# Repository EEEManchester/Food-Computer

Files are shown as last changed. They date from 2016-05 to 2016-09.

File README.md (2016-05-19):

# Food-Computer
A project to create a controlled indoor growing environment using embedded systems, sensors and control

Our plan is to build a www.eee.manchester.ac.uk  prototype version of the MIT OpenAgri "Food Computer" with an idea to scaling the design out in the future. 

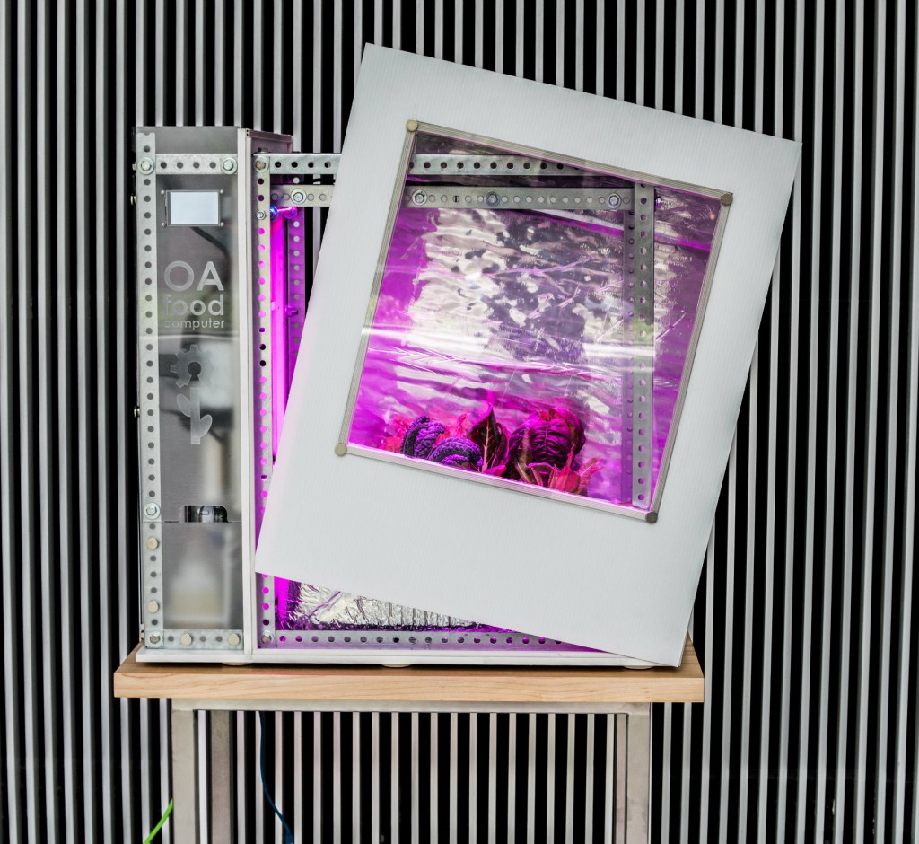
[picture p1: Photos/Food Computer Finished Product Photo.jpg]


####Please see our Github Wiki for all information on the project

Code and hardware are forked from https://github.com/OpenAgInitiative

For more information see here
https://www.media.mit.edu/special/groups/open-ag

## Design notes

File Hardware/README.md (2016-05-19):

# gro-hardware
All things related to assembling a food computer. CAD Models, Build Manual, Bill of Materials, etc.

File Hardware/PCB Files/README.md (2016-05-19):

# gro-PCB
Robusto board, RHC12, and RHC12-BTA schematics/pcbs

Robusto is split into two parts, Part1 and Part2.  RHC12 is the base connector that works with Grove and 0.1" spaced header, RHC12-BTA is for a BTA connector.  

##THESE PCBS HAVE BEEN CONVERTED TO ALTIUM DESIGNER BY EEE MANCHESTER FROM EAGLE BOARD FILES CREATED AT MIT

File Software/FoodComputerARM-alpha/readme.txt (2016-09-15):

Alpha version; tested only on ARM mbed Nucleo F401RE board.
Can be found here: 
https://developer.mbed.org/users/AfdhalAtiffTan/code/FoodComputerARM-alpha/

It meant to replace Arduino boards and use ARM processor instead.
It serves the same purpose as "Food_Computer_Draft_V2" (with compatible pinout).

Differences:
-It uses MODBUS RTU instead of non-standard uart protocol.
-Analogue pins are 3.3V, make sure to divide the voltage first.
-Has three debugging LEDs.
-Some of the sensors data were scaled by 100;

Logs:
-Tried to use RTOS, but failed because the software-serial library can't handle it (took a long time to figure this out).

-Because RTOS failed, it uses Ticker instead.

-Most of the libraries are download from mbed community.

-The modbus library was a modified Arduino library.

-Programming using ST-Link achieves more consistent results.

-Sometimes, the online compiler gives peculiar result, try to compile using Keil (by exporting it to local pc). In other words, sometimes, both online and Keil compiler can give very different behaviour (such as failed I2C etc.). 

-If uses mbed to upload the program, don't forget to manually reset the ARM board by pushing the reset button before every each upload. Not too sure why but it was discovered that it gives more predictable result.

-Reconnecting the USB cable and Clicking on "Compile" then "Compile All" multiple times sometimes helps.

-If errors were found, sometimes clicking the "Update" and "Update All" helps. 

-All of the communications tested only on oscilloscope, not on the actual sensors.

-The program will not start without CO2 sensor because of the blocking-call used.

-Don't request data faster than 1 second because the update rate is 100ms (not including sensors).

-Searching library/program on the mbed IDE gives incomplete results. Better to use mbed website or Google.

Notes:
-Program here was exported from mbed environment.
-The program is far from perfect, bugs might exists. 
-It was not written to look proper, yet.
-The code may look ugly as it was coded using the glue method.
-If the Raspberry Pi appears not to be stuck, add a 5 seconds delay after relay initialisation. Fault from: Modbus library.

To-dos:
-Proper documentation and Doxygen.
-Format the code so that it looks more professional and manageable.
-Test all communication on all sensors.

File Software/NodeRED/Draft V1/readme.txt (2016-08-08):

This Draft V1 is meant for backup purposes. It is far from ideal and may contains a lot of bugs.

It should be able to control arduino (or any capable microcontroller) via serial communication (onboard usb-ttl).
 
It has:
-simple relay control
-simple relay timer
-non-standard serial communication (simple one-character ascii commands)
-charts for sensors (polled every 10 seconds)
-gauges for sensor (polled every 10 seconds)
-simple webcam interface (just live stream, no capture yet)
-simple close-loop control (bang-bang controller) for lights, humidity and temperature
-simple MQTT client
-basic system control (Pi reboot and shutdown)

To use it, simply install nodered by using [Peter Scargill]'s scripts:

https://bitbucket.org/snippets/scargill/ayAG6/include-for-jessie-script-call-it

https://bitbucket.org/snippets/scargill/L8zjE/raspbian-jessie-and-node-red-script-for

For installation explanation by [Peter Oakes] (near minute 9:30):
https://www.youtube.com/watch?v=uyx2KZNxhe4

The installation should include all required libraries. If not, they can be found on:
http://flows.nodered.org/ or
https://www.npmjs.com/

Optional: "Motion" package must be installed on the Pi in order to use the usb webcam:
https://pimylifeup.com/raspberry-pi-webcam-server/

After installation, node-red can be access via:
main interface: http://localhost:1880
web UI: http://localhost:1880/ui

Then, import the json file (flows_FoodComputerPi.json) by copying and paste it into (localhost:1880)>(Menu)>(Import)>(Clipboard)

Optional: Port forwarding, to allow external access.

Future version:
-Should include modbus-rtu. Credit: [Sam Walsh].

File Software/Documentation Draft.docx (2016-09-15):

# Microcontroller Connections

Any microcontroller that has the ability to interface with all of the listed sensors can be used, but, at the moment (August 2016), only two test programs were pushed on this repository:

- “Food_Computer_Draft_V2” sketch: For Arduino based boards (such as Uno, Mega, Nano, etc).
- “FoodComputerARM-alpha” program: For mbed-enabled ARM-based boards (tested only on Nucleo F401RE) – uses.

Feel free to use any other suitable microcontroller as needed.

Main tasks of the microcontroller are reading all sensors and controlling relays via UART.

No intelligence implemented yet (such as fail-safe, auto scheduling, RTC based timer, closed-loop control, etc). All controls are manually controlled.

Actuators were controlled by Relay modules.

Sensors Used:

- Carbon Dioxide Sensor (http://www.co2meter.com/products/cozir-0-2-co2-sensor): COZIR Ambient 2/5/10K CO2 Sensor [UART]
- Air Humidity and Temperature Sensor (https://www.seeedstudio.com/item_detail.html?p_id=838): Grove - Temperature&Humidity Sensor Pro (DHT22) [AM2302]
- Light Intensity Sensor (https://www.seeedstudio.com/item_detail.html?p_id=1281): Grove - Digital Light Sensor (TSL2561) [I2C]
- Water pH Sensor (http://www.dfrobot.com/index.php?route=product/product&product_id=1025): Gravity: Analog pH Meter Kit [ADC]
- Temperature compensated Water Conductivity Sensor (http://www.dfrobot.com/index.php?route=product/product&product_id=1123): Gravity:Analog Electrical Conductivity Meter (With Temperature Compensation (http://www.dfrobot.com/index.php?route=product/product&product_id=689)) [ADC for EC and 1-Wire for DS18B20 thermometer]

Both analogue sensors have voltage divider (from 5V to 3.3V) hidden in cables (heat shrink tube) to avoid damaging 3.3V ARM board (Arduino runs on 5V). The resistors used were 1% tolerance and 3.3kR, 100R and 1.6kR all in series.

Physical Pinouts:

Both Arduino and mbed uses Arduino’s pin convention, A and D stands for Analog and Digital pin respectively.

(Compatible with “Food_Computer_Draft_V2” and “FoodComputerARM-alpha”)

A0 – Water pH Sensor (Analog) – 5V

A1 – Water Electrical Conductivity Sensor (Analog) – 5V

A2 – Shell Switch (Digital) – 5V or 3.3V on ARM

A3 – Window Switch (Digital) – 5V or 3.3V on ARM

D0 – Reserved for USB/UART communication (RX)

D1 – Reserved for USB/UART communication (TX)

D2 – Air Humidity and Temperature Sensor (DHT22) – 5V

D3 – Water Temperature Sensor (OneWire) – 5V

D4 – Relay0 (Active Low) – AC – Grow Light - 240V

D5 – Relay1 (Active Low) – AC – Water Pump - 240V

D6 – Relay2 (Active Low) – AC – Air Pump - 240V

D7 – Relay3 (Active Low) – AC – Air Pump - 240V

D8 – Relay4 (Active Low) – DC – Circulation Fan - 12V

D9 – Relay5 (Active Low) – DC – Ventilation Fan - 12V

D10 – Relay6 (Active Low) – DC – Strip Lights - 12V

D11 – Relay7 (Active Low) – DC – Air Humidifier - 5V

D12 – CO2 Sensor (RX) - 3.3V!

D13 – CO2 Sensor (TX) - 3.3V!

D14 – Light intensity sensor (SDA) – 5V

D15 – Light intensity sensor (SCL) – 5V

Connections were done via Grove Shield v2 (http://wiki.seeedstudio.com/wiki/Grove_-_Base_shield_v2).

If troubleshooting the connection via the connectors on the shield, the silkscreens on the PCB represent:

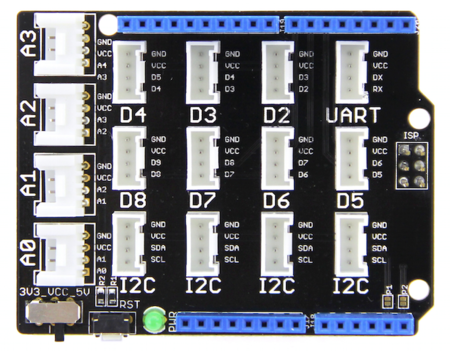
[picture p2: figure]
caption

Image credit: Google image search

Vcc switch was set 5V. RST button is useful especially if raspberry pi or the Modbus library stuck.

UART – 5V power to relay module 1

D2- Air Humidity and Temperature Sensor (DHT22)

D3 - Water Temperature Sensor (OneWire)

D4 – 5V power to relay module 2

A0 – pH Sensor

A1 – EC Sensor

A2 – Windows Switch Sensor

A3 – Shell Switch Sensor

I2C (any port would do) – Light Intensity Sensor

To reset the microcontroller board via Raspberry Pi, an open-collector npn switch was connected to GPIO BCM16 (or GPIO16 or pin 36) on the Pi.

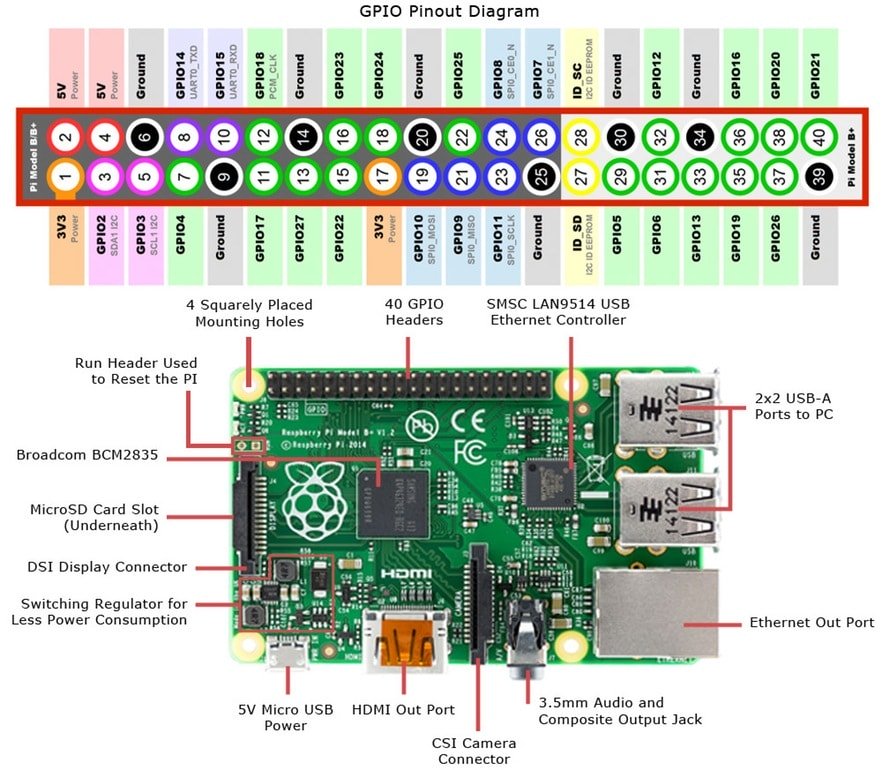
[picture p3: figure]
Image result for raspberry pi 3 pinout

Image credit: google image search

# Developed Firmwares:

As mentioned above, there are two firmwares listed in this repo:

Food_Computer_Draft_V2

Is a simple Arduino based “sketch”. It comes with simple Python PyQt based GUI that sends simple non-standard ascii-commands through USB/UART. Sensor readings were sent in CSV format.

The sketch is nothing but a combined libraries that read all attached sensors and send it to COM port.

FoodComputerARM-alpha

Developed using mbed compiler. Coded to be controlled by 9600 baud-rate MODBUS-RTU (credit: Sam). Sensor readings can be extracted by using Modbus register read command (http://www.simplymodbus.ca/FC03.htm).

The Nucleo-401RE board is configured as Modbus slave and its address is 01.

The register used are as follows:

Holding Register Address | Stored Data | Comment
01 | Carbon Dioxide Sensor (the sensor is also at 9600bps) | PPM Value
02 | Air Humidity Sensor (DHT22 protocol) | In % (scaled to x100)
03 | Air Temperature (via humidity sensor) | In Celcius (scaled to x100)
04 | Water Temperature (OneWire) | In Celcius (scaled to x100)
05 | Water Electrical Conductivity (Analogue) | In mS/cm (scaled to x100)
06 | Water pH Level (Analogue) | In pH (scaled to x100)
07 | Light Intensity (I2C) | Lux?
08 | Window Switch | Simple True/False
09 | Shell Switch (should be used for water level instead?) | Simple True/False
10 | Relays (should be changed in future so that individual relays has its own register) | Use this register to control relays (first bit is for first relay, second bit is for second relay, and so on)

The Modbus library works by periodically checks for request every 100ms. Meaning, any data transactions must be no faster than 100ms. This can be modified to run on separate thread, but, other library incompatibly issues will arise. Future revision should use a more robust Modbus library (UART interrupts?).

# Developed GUIs (PyQT-based)

- Simple UART
- Simple MQTT
- Simple Node-Red web UI (for ARM and Arduino)

(to be continued…)

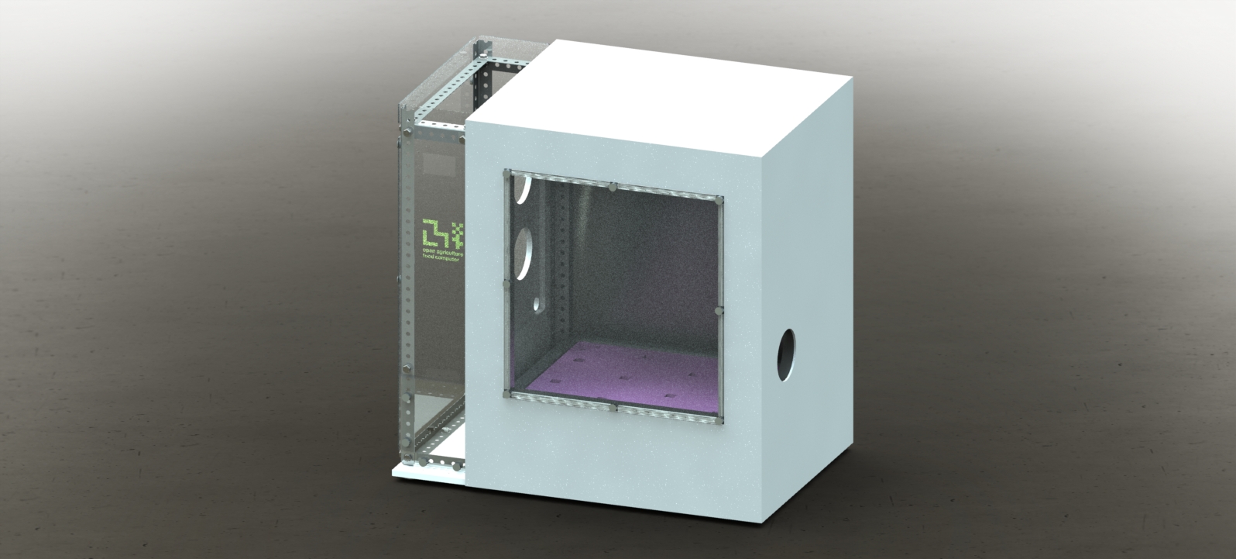
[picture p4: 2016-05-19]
Hardware/Food Computer CAD/RENDERS/Iso Closed.JPG

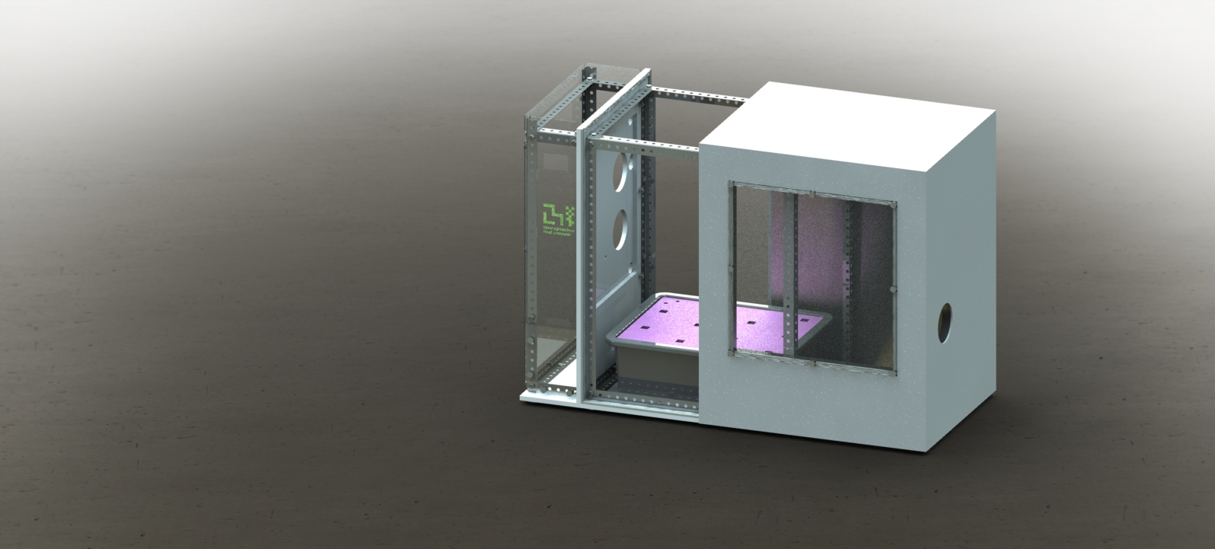
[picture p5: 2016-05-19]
Hardware/Food Computer CAD/RENDERS/Iso Brighter.JPG

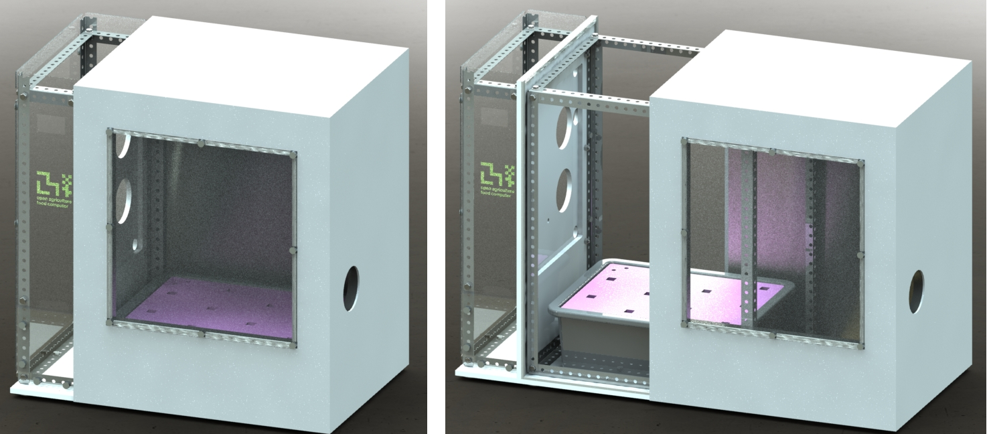
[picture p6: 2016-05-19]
Hardware/Food Computer CAD/RENDERS/Compilation.png

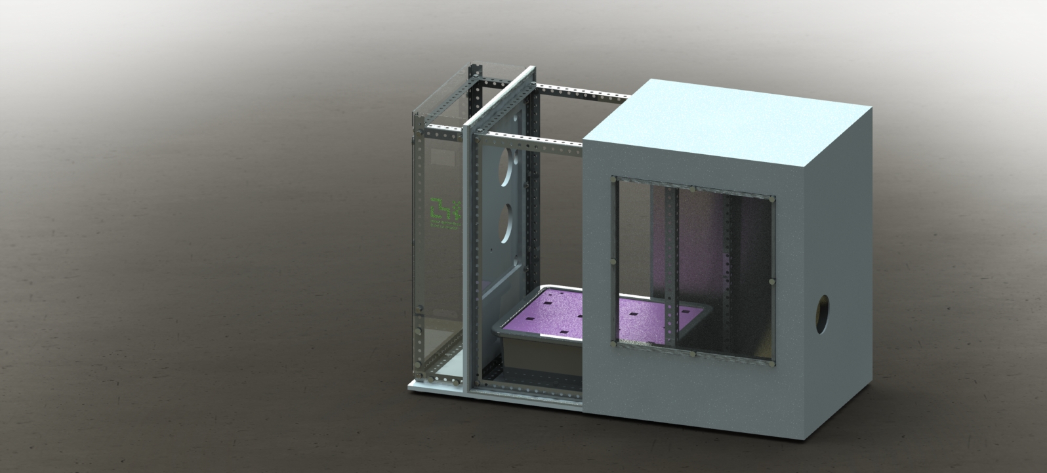
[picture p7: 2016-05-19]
Hardware/Food Computer CAD/RENDERS/Iso.JPG

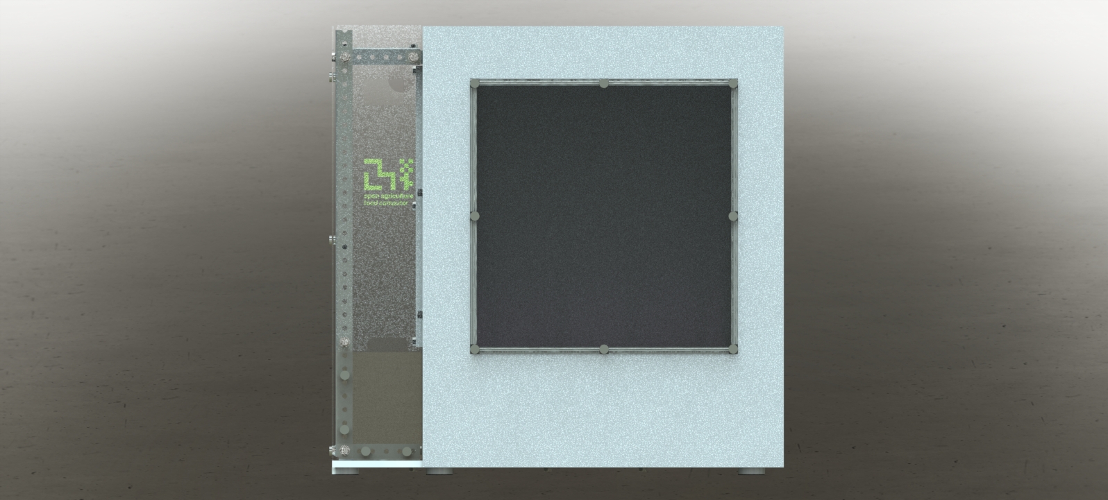
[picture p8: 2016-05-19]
Hardware/Food Computer CAD/RENDERS/Front Closed.JPG

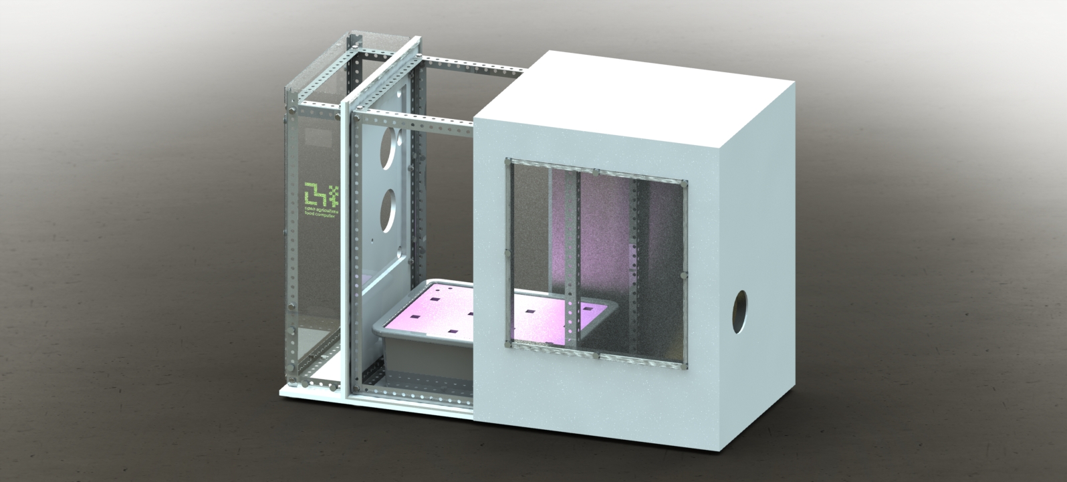
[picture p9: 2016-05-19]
Hardware/Food Computer CAD/RENDERS/Iso Brightest.JPG

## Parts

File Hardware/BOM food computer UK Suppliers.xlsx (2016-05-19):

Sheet: Motherboard University Supplier
Item Name | Distributor | Distributor's Item Name | Units | Cost per Unit ($) | Item Cost | Ordered
POWER
Power Strip (http://www.uk.insight.com/en-gb/productinfo/power-adapters/0003849924) | Insight | Belkin 6 Outlet Power Surge Protector | 1 | £9.26 | £9.26
Main Power Supply (https://www.amazon.co.uk/sourcingmap-Input-Output-Metallic-Supply/dp/B00E0K8LXO) | AmazonPrime | 12V 30A 360W Switching Power Supply for LED Strip Light | 1 | £20.10 | £20.10
BRAINS
Raspberry Pi 3 Essentials Kit (https://shop.pimoroni.com/products/raspberry-pi-3-essentials-kit?) | Pimoroni | CanaKit 5V 2.5A Raspberry Pi 2 Power Supply (UL Listed) | 1 | £52.00 | £52.00
Arduino Mega 2560 (http://uk.farnell.com/arduino/a000067/atmega2560-arduino-mega2560-rev3/dp/2212779) | Farnell | Arduino Mega 2560 R3 for Arduino | 1 | £28.76 | £28.76
Arduino Mega Protoshield (http://onecall.farnell.com/arduino/a000077/arduino-shield-proto-shield/dp/SC13010) | Farnell | ARDUINO A000077 ARDUINO SHIELD, PROTO SHIELD | 1 | £14.00 | £14.00
Grove Base Shield (http://www.seeedstudio.com/depot/Base-Shield-V2-p-1378.html) | SeeedStudio | Base Shield V2 | 1 | 8.9 | 8.9
Touchscreen Display (https://shop.pimoroni.com/products/pitft-plus-480x320-3-5-tft-touchscreen-for-raspberry-pi-pi-2-and-model-a-b) | Pimoroni | PiTFT - Assembled 480x320 3.5" TFT+Touchscreen for Raspberry Pi | 1 | £39.00 | £39.00
GPIO Cable (http://onecall.farnell.com/cyntech/ctlgpiopi-01/raspberry-pi-gpio-ribbon-100mm/dp/SC12819) | Farnell | GPIO ribbon cable for Raspberry Pi set with 2x13 stackable header and 2x13 box header | 1 | £1.19 | £1.19
VOLTAGE CONTROL
4-Channel Relay (https://www.amazon.co.uk/Shield-Module-channels-optocoupler-Arduino/dp/B00X3VRMPY) | AmazonPrime UK | JBtek 4 Channel DC 5V Relay Module for Arduino Raspberry Pi DSP AVR PIC ARM | 2 | £6.99 | £13.98
AC Relay 2 Plug Outlet (https://www.amazon.co.uk/Masterplug-NBS22UB-Brushed-Socket-Charger/dp/B00KMVYJX6) | AmazonPrime UK | Masterplug NBS22UB Brushed Steel Twin Socket with USB Charger | 2 | £14.95 | £29.90
AC Relay 2 gang back box (https://www.amazon.co.uk/Gang-Metal-Flush-Mount-Pattress/dp/B01BLFS8N8?rps=1) | AmazonPrime UK | 5x 2 GANG METAL BACK BOX | 1 | £7.99 | £7.99
LIGHTS
White LED Strip (https://www.amazon.co.uk/Waterproof-Flexible-Lights-3528-Daylight/dp/B00HSF66JO) | AmazonPrime UK | Triangle Bulbs T93007 - Waterproof Flexible LED Strip Light, 300 LED's, 3528 SMD, Pure White, 16.4 feet / 5M | 2 | £9.99 | £19.98
Grow LED Panel (https://www.amazon.co.uk/dp/B00W54BHO2?colid=E7891C74300P&coliid=I3MK2UTDFRU1HX) | AmazonPrime UK | Erligpowht 45W LED Red Blue Indoor Garden Plant Grow Light Hanging Light | 2 | £27.99 | £55.98
AIR CONDITIONING
Heater (https://www.amazon.co.uk/Honeywel-Personal-Heater/dp/B01BSEY5LQ) | AmazonPrime UK | HoneyWell Personal Ceramic Heater | 1 | £24.99 | £24.99
Humidifier (https://www.amazon.co.uk/FOME-Portable-Bottle-Humidifier-bottle/dp/B00X3GA5JO) | AmazonPrime UK | FOME Portable Bottle Cap Air Humidifier | 1 | £8.99 | £8.99
USB Wall Adapter (https://www.amazon.co.uk/PIXNOR-UK-plug-Output-Adapter-Charger/dp/B00IVC8U24) | AmazonPrime UK | PIXNOR 5V/2A UK-plug Dual USB Output AC Power Adapter Wall Charger | 3 | £4.99 | £14.97
Circulation/Vent Fans (https://www.amazon.co.uk/VIKINS-Delta-AFB1212VHE-cooling-Connector/dp/B01EURAYC2?s=computers) | AmazonPrime UK | VIKINS Delta AFB1212VHE 120mm X 38mm Very High Speed cooling Fan 2Pin 2 wire Connector 148 CFM NEW | 2 | £10.99 | £21.98
Fan Guards (https://www.amazon.co.uk/Silver-Axial-Protector-Finger-Guards/dp/B007PPEPJ0?s=computers) | AmazonPrime UK | 5 Pcs Silver Tone Axial Fan Grill Protector 12cm Metal Finger Guards | 1 | £5.43 | £5.43
Fan Louvres (https://www.amazon.co.uk/Kair-Gravity-Grille-Ventilation-DUCVKC243-BK/dp/B004X4RWJG) | AmazonPrime UK | Kair Gravity Grille - 100mm Round Spigot - Black - SYS-100 Ducting 4 inch Plastic Air Vent PVC Ventilation Duct Shutter Flap Non-Return Outlet Gravity Grill DUCVKC243-BK | 2 | £5.49 | £10.98
ENVIRONMENTAL SENSING
CO2 Sensor (http://www.co2meter.com/products/cozir-0-2-co2-sensor) | CO2Meter.com | COZIR Ambient 5K CO2 Sensor | 1 | $109.00 | $109.00 | Looks like only supplier available
Air Temperature and Humidity Sensor (https://www.amazon.co.uk/SeeedStudio-Temperature-Capacitive-Measurement-Compensation/dp/B00WX2BI5E) | AmazonPrime UK | Grove - Temperature&Humidity Sensor Pro | 1 | £16.99 | £16.99
Light Intensity Sensor (http://www.seeedstudio.com/depot/Grove-Digital-Light-Sensor-p-1281.html) | SeeedStudio | Grove - Digital Light Sensor | 1 | 9.9 | 9.9 | Available on Amazon but not prime
Webcam (https://www.amazon.co.uk/ELP-Camera-Megapixel-Windows-Android/dp/B00KA7WSSU) | AmazonPrime UK | ELP 2.1mm Lens Wide Angle Webcam Low Illumination USB Camera Module for Day&night Linux Vision | 1 | £35.60 | £35.60
ENCLOSURE SENSING
Magnetic Switch (https://www.amazon.co.uk/MC-31B-Optional-Sensor-Magnetic-Contact/dp/B00O9YULGQ) | AmazonPrime UK | Magnetic Switch | 1 | £7.33 | £7.33
Limit Switch (https://www.amazon.co.uk/Micro-Limit-Switch-Straight-Action/dp/B00H53DUHA) | AmazonPrime UK | 10 Pcs Mini Micro Limit Switch Roller Lever Arm SPDT Snap Action LOT | 1 | £5.60 | £5.60
WATER CONDITIONING
Air Pump (https://www.amazon.co.uk/Tetra-T281-APS50-Air-Pump/dp/B0055F7G0C) | AmazonPrime UK | Tetra Whisper Air Pump APS50 | 1 | £11.95 | £11.95
Air Stone (https://www.amazon.co.uk/Gray-Round-Shape-Airstone-Aquarium/dp/B008MP019U) | Amazon UK (non prime) | Gray Round Shape Air Pump Airstone for Aquarium Tank Fish | 1 | £1.12 | £1.12
Air Pump Tubing (https://www.amazon.co.uk/Aquarium-Clear-White-Silicon-Line/dp/B009IS90HY) | AmazonPrime UK | Aquarium 6M x 5mm Clear White Silicon Air Line Pond Pump Fish Tube Pipe | 1 | £6.22 | £6.22
Aquarium Pump (https://www.amazon.co.uk/Submersible-Water-Aquarium-Powerhead-Hydroponics/dp/B014W91OOK) | AmazonPrime UK | VicTsing 80 GPH Submersible Hydroponics Aquaponics Statuary Water Fountain Pump | 1 | £9.59 | £9.59
Pump Tubing (https://www.amazon.co.uk/Hozelock-13-25-Supply-Hose/dp/B0016OZFTK) | AmazonPrime UK | Hozelock 13 mm x 25 m Supply Hose | 1 | £20.45 | £20.45
WATER SENSING
Water Temperature and EC Sensor (http://www.dfrobot.com/index.php?route=product/product&product_id=1123&search=DFR0300#.VdTDoFNViko) | RobotShop | Analog Electrical Conductivity Meter (With Temperature Compensation) | 1 | £48.54 | £48.54
pH Sensor (http://www.dfrobot.com/index.php?route=product/product&product_id=1025#.Vg60SBNViko) | RobotShop | Analog pH Meter Kit | 1 | £20.18 | £20.18
ENCLOSURES
Cable Management Box (https://www.amazon.co.uk/ORICO%C2%AE-Adapter-Management-Storage-Box-PB3218/dp/B01C81BROG) | AmazonPrime UK | ORICO PB3218 Power Strip Cord Management Box Cable Box Cable Storage Box (Black) | 1 | £15.00 | £15.00
ADDITIONAL COMPONENTS
Sacrificial AC Extension Cable for high gauge wire | AmazonPrime | C2G / Cables To Go 53408 18 AWG Outlet Saver Power Extension Cord for NEMA 5-15P to NEMA 5-15R, Black (12 Feet/3.65 Meters) | 1 | 10.93 | 10.93
Wago Lever Nut Assortment (https://www.amazon.co.uk/WAGO-compact-connector-Cross-section-Stranded/dp/B000JJPA66) | AmazonPrime UK | Wago (25) 222-412 (25) 222-413 (20) 222-415 Lever-Nut Assortment Pack | 1 | 39.99 | 39.99
Heat Shrink Tubing (http://www.amazon.com/Vktech-150pcs-Shrink-Tubing-Sleeving/dp/B00EXLPLTW) | AmazonPrime | Vktech 150pcs 2:1 Heat Shrink Tubing Tube Sleeving Wire Cable 8 Sizes 2-13mm Black | 1 | 6.2 | 6.2
Grove Cables (http://www.seeedstudio.com/depot/Grove-c-98_106_57/?ref=crumb) | SeeedStudio | Buy an assortment of 10-50cm grove cables for this build. The 50cm cables
 |  | are better for the sensors and the shorter cables can be used as needed.
Foam mounting tape (http://www.homedepot.com/p/3M-Scotch-1-in-x-12-5-yds-Indoor-Outdoor-Mounting-Tape-411-LONG-DC/100153200) | Home Depot | Foam Mounting Tape | 1 | 15.97 | 15.97
Electrical Tape (http://www.amazon.com/3M-Electrical-75-Inch-66-Foot-0085-Inch/dp/B00004WCCP?s=industrial) | Amazon | Electrical Tape | 1 | 3.98 | 3.98
Air Exchange Box (http://www.digikey.com/product-search/en?KeyWords=377-2132-ND&WT.z_header=search_go) | Digikey | Plastic Box | 1 | 29.5 | 29.5
Short Screws (http://www.homedepot.com/p/Everbilt-6-x-1-2-in-Stainless-Steel-Pan-Head-Phillips-Sheet-Metal-Screw-50-per-Pack-800162/204275035) | Home Depot | #6 x 1/2 in. Stainless Steel Pan-Head Phillips Sheet Metal Screw (50 per Pack) | 1 | 5.8 | 5.8
Long Screws (http://www.homedepot.com/p/Everbilt-8-x-2-in-Zinc-Plated-Pan-Head-Phillips-Drive-Sheet-Metal-Screw-50-Piece-801632/204275094) | Home Depot | #8 x 2 in. Zinc-Plated Pan-Head Phillips Drive Sheet Metal Screw (50-Piece) | 1 | 3.51 | 3.51
TOTAL COMPONENTS |  |  | 50 | 826.72 | 826.72

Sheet: Motherboard UK
Item Name | Distributor | Distributor's Item Name | Units | Cost per Unit ($) | Item Cost
POWER
Power Strip (http://www.amazon.com/CyberPower-CSB606-Protector-6-Outlets-Joules/dp/B00FLTTGYG) | AmazonPrime | CyberPower CSB606 Surge Protector 6-Outlets 6-Ft Cord 900 Joules | 1 | 10.15 | 10.15 |  | Belkin 6 Outlet Power Surge Protector - surge protector | 9.26
Main Power Supply (https://www.amazon.co.uk/sourcingmap-Input-Output-Metallic-Supply/dp/B00E0K8LXO) | AmazonPrime | 12V 30A 360W Switching Power Supply for LED Strip Light | 1 | £20.10 | £20.10
AC Extension Cable (http://www.amazon.com/gp/product/B0002J1KS0/ref=ox_sc_act_title_1?ie=UTF8&psc=1&smid=ATVPDKIKX0DER) | AmazonPrime | C2G / Cables To Go 03137 18 AWG Outlet Saver Power Extension Cord for NEMA 5-15P to NEMA 5-15R, Black (1 Foot/0.30 Meters) | 1 | 4.99 | 4.99
BRAINS
Raspberry Pi 3 Essentials Kit (https://shop.pimoroni.com/products/raspberry-pi-3-essentials-kit?) | Pimoroni | CanaKit 5V 2.5A Raspberry Pi 2 Power Supply (UL Listed) | 1 | £52.00 | £52.00
Arduino Mega 2560 (https://www.amazon.co.uk/Arduino-Mega-2560-R3-Microcontroller/dp/B0046AMGW0) | AmazonPrime | Arduino Mega 2560 R3 for Arduino | 1 | £27.99 | £27.99
Arduino Mega Protoshield (https://www.amazon.co.uk/PROTO-SHIELD-Arduino-Prototyping-shield-buttons/dp/B018F1V0MW?rps=1) | AmazonPrime UK | Gikfun Protoshield Prototype Shield DIY KIT A1 for Arduino Mega 1280 2560 R1 - R3 | 1 | £14.00 | £14.00
Grove Base Shield (http://www.seeedstudio.com/depot/Base-Shield-V2-p-1378.html) | SeeedStudio | Base Shield V2 | 1 | 8.9 | 8.9
Touchscreen Display (https://shop.pimoroni.com/products/pitft-plus-480x320-3-5-tft-touchscreen-for-raspberry-pi-pi-2-and-model-a-b) | Pimoroni | PiTFT - Assembled 480x320 3.5" TFT+Touchscreen for Raspberry Pi | 1 | £39.00 | £39.00
GPIO Cable (http://www.amazon.com/ribbon-cable-Raspberry-stackable-header/dp/B00G84WNA2) | AmazonPrime | GPIO ribbon cable for Raspberry Pi set with 2x13 stackable header and 2x13 box header | 1 | 3.99 | 3.99
VOLTAGE CONTROL
4-Channel Relay (https://www.amazon.co.uk/Shield-Module-channels-optocoupler-Arduino/dp/B00X3VRMPY) | AmazonPrime UK | JBtek 4 Channel DC 5V Relay Module for Arduino Raspberry Pi DSP AVR PIC ARM | 2 | £6.99 | £13.98
AC Relay 2 Plug Outlet (https://www.amazon.co.uk/Masterplug-NBS22UB-Brushed-Socket-Charger/dp/B00KMVYJX6) | AmazonPrime UK | Masterplug NBS22UB Brushed Steel Twin Socket with USB Charger | 2 | £14.95 | £29.90
AC Relay 2 gang back box (https://www.amazon.co.uk/Gang-Metal-Flush-Mount-Pattress/dp/B01BLFS8N8?rps=1) | AmazonPrime UK | 5x 2 GANG METAL BACK BOX | 1 | £7.99 | £7.99
LIGHTS
White LED Strip (https://www.amazon.co.uk/Waterproof-Flexible-Lights-3528-Daylight/dp/B00HSF66JO) | AmazonPrime UK | Triangle Bulbs T93007 - Waterproof Flexible LED Strip Light, 300 LED's, 3528 SMD, Pure White, 16.4 feet / 5M | 2 | £9.99 | £19.98
Grow LED Panel (https://www.amazon.co.uk/dp/B00W54BHO2?colid=E7891C74300P&coliid=I3MK2UTDFRU1HX) | AmazonPrime UK | Erligpowht 45W LED Red Blue Indoor Garden Plant Grow Light Hanging Light | 2 | £27.99 | £55.98
AIR CONDITIONING
Heater (https://www.amazon.co.uk/Honeywel-Personal-Heater/dp/B01BSEY5LQ) | AmazonPrime UK | HoneyWell Personal Ceramic Heater | 1 | £24.99 | £24.99
Humidifier (https://www.amazon.co.uk/FOME-Portable-Bottle-Humidifier-bottle/dp/B00X3GA5JO) | AmazonPrime UK | FOME Portable Bottle Cap Air Humidifier | 1 | £8.99 | £8.99
USB Wall Adapter (https://www.amazon.co.uk/PIXNOR-UK-plug-Output-Adapter-Charger/dp/B00IVC8U24) | AmazonPrime UK | PIXNOR 5V/2A UK-plug Dual USB Output AC Power Adapter Wall Charger | 3 | £4.99 | £14.97
Circulation/Vent Fans (https://www.amazon.co.uk/VIKINS-Delta-AFB1212VHE-cooling-Connector/dp/B01EURAYC2?s=computers) | AmazonPrime UK | VIKINS Delta AFB1212VHE 120mm X 38mm Very High Speed cooling Fan 2Pin 2 wire Connector 148 CFM NEW | 2 | £10.99 | £21.98
Fan Guards (https://www.amazon.co.uk/Silver-Axial-Protector-Finger-Guards/dp/B007PPEPJ0?s=computers) | AmazonPrime UK | 5 Pcs Silver Tone Axial Fan Grill Protector 12cm Metal Finger Guards | 1 | £5.43 | £5.43
Fan Louvres (https://www.amazon.co.uk/Kair-Gravity-Grille-Ventilation-DUCVKC243-BK/dp/B004X4RWJG) | AmazonPrime UK | Kair Gravity Grille - 100mm Round Spigot - Black - SYS-100 Ducting 4 inch Plastic Air Vent PVC Ventilation Duct Shutter Flap Non-Return Outlet Gravity Grill DUCVKC243-BK | 2 | £5.49 | £10.98
ENVIRONMENTAL SENSING
CO2 Sensor (http://www.co2meter.com/products/cozir-0-2-co2-sensor) | CO2Meter.com | COZIR Ambient 5K CO2 Sensor | 1 | $109.00 | $109.00 | Looks like only supplier available
Air Temperature and Humidity Sensor (https://www.amazon.co.uk/SeeedStudio-Temperature-Capacitive-Measurement-Compensation/dp/B00WX2BI5E) | AmazonPrime UK | Grove - Temperature&Humidity Sensor Pro | 1 | £16.99 | £16.99
Light Intensity Sensor (http://www.seeedstudio.com/depot/Grove-Digital-Light-Sensor-p-1281.html) | SeeedStudio | Grove - Digital Light Sensor | 1 | 9.9 | 9.9 | Available on Amazon but not prime
Webcam (https://www.amazon.co.uk/ELP-Camera-Megapixel-Windows-Android/dp/B00KA7WSSU) | AmazonPrime UK | ELP 2.1mm Lens Wide Angle Webcam Low Illumination USB Camera Module for Day&night Linux Vision | 1 | £35.60 | £35.60
ENCLOSURE SENSING
Magnetic Switch (https://www.amazon.co.uk/MC-31B-Optional-Sensor-Magnetic-Contact/dp/B00O9YULGQ) | AmazonPrime UK | Magnetic Switch | 1 | £7.33 | £7.33
Limit Switch (https://www.amazon.co.uk/Micro-Limit-Switch-Straight-Action/dp/B00H53DUHA) | AmazonPrime UK | 10 Pcs Mini Micro Limit Switch Roller Lever Arm SPDT Snap Action LOT | 1 | £5.60 | £5.60
WATER CONDITIONING
Air Pump (https://www.amazon.co.uk/Tetra-T281-APS50-Air-Pump/dp/B0055F7G0C) | AmazonPrime UK | Tetra Whisper Air Pump APS50 | 1 | £11.95 | £11.95
Air Stone (https://www.amazon.co.uk/Gray-Round-Shape-Airstone-Aquarium/dp/B008MP019U) | Amazon UK (non prime) | Gray Round Shape Air Pump Airstone for Aquarium Tank Fish | 1 | £1.12 | £1.12
Air Pump Tubing (https://www.amazon.co.uk/Aquarium-Clear-White-Silicon-Line/dp/B009IS90HY) | AmazonPrime UK | Aquarium 6M x 5mm Clear White Silicon Air Line Pond Pump Fish Tube Pipe | 1 | £6.22 | £6.22
Aquarium Pump (https://www.amazon.co.uk/Submersible-Water-Aquarium-Powerhead-Hydroponics/dp/B014W91OOK) | AmazonPrime UK | VicTsing 80 GPH Submersible Hydroponics Aquaponics Statuary Water Fountain Pump | 1 | £9.59 | £9.59
Pump Tubing (https://www.amazon.co.uk/Hozelock-13-25-Supply-Hose/dp/B0016OZFTK) | AmazonPrime UK | Hozelock 13 mm x 25 m Supply Hose | 1 | £17.50 | £17.50
WATER SENSING
Water Temperature and EC Sensor (http://www.dfrobot.com/index.php?route=product/product&product_id=1123&search=DFR0300#.VdTDoFNViko) | DFRobot | Analog Electrical Conductivity Meter (With Temperature Compensation) | 1 | 69.9 | 69.9
pH Sensor (http://www.dfrobot.com/index.php?route=product/product&product_id=1025#.Vg60SBNViko) | DFRobot | Analog pH Meter Kit | 1 | 29.5 | 29.5
ENCLOSURES
Cable Management Box (https://www.amazon.co.uk/ORICO%C2%AE-Adapter-Management-Storage-Box-PB3218/dp/B01C81BROG) | AmazonPrime UK | ORICO PB3218 Power Strip Cord Management Box Cable Box Cable Storage Box (Black) | 1 | £15.00 | £15.00
ADDITIONAL COMPONENTS
Sacrificial AC Extension Cable for high gauge wire | AmazonPrime | C2G / Cables To Go 53408 18 AWG Outlet Saver Power Extension Cord for NEMA 5-15P to NEMA 5-15R, Black (12 Feet/3.65 Meters) | 1 | 10.93 | 10.93
Wago Lever Nut Assortment (https://www.amazon.co.uk/WAGO-compact-connector-Cross-section-Stranded/dp/B000JJPA66) | AmazonPrime UK | Wago (25) 222-412 (25) 222-413 (20) 222-415 Lever-Nut Assortment Pack | 1 | 39.99 | 39.99
Heat Shrink Tubing (http://www.amazon.com/Vktech-150pcs-Shrink-Tubing-Sleeving/dp/B00EXLPLTW) | AmazonPrime | Vktech 150pcs 2:1 Heat Shrink Tubing Tube Sleeving Wire Cable 8 Sizes 2-13mm Black | 1 | 6.2 | 6.2
Grove Cables (http://www.seeedstudio.com/depot/Grove-c-98_106_57/?ref=crumb) | SeeedStudio | Buy an assortment of 10-50cm grove cables for this build. The 50cm cables
 |  | are better for the sensors and the shorter cables can be used as needed.
Foam mounting tape (http://www.homedepot.com/p/3M-Scotch-1-in-x-12-5-yds-Indoor-Outdoor-Mounting-Tape-411-LONG-DC/100153200) | Home Depot | Foam Mounting Tape | 1 | 15.97 | 15.97
Electrical Tape (http://www.amazon.com/3M-Electrical-75-Inch-66-Foot-0085-Inch/dp/B00004WCCP?s=industrial) | Amazon | Electrical Tape | 1 | 3.98 | 3.98
Air Exchange Box (http://www.digikey.com/product-search/en?KeyWords=377-2132-ND&WT.z_header=search_go) | Digikey | Plastic Box | 1 | 29.5 | 29.5
Short Screws (http://www.homedepot.com/p/Everbilt-6-x-1-2-in-Stainless-Steel-Pan-Head-Phillips-Sheet-Metal-Screw-50-per-Pack-800162/204275035) | Home Depot | #6 x 1/2 in. Stainless Steel Pan-Head Phillips Sheet Metal Screw (50 per Pack) | 1 | 5.8 | 5.8
Long Screws (http://www.homedepot.com/p/Everbilt-8-x-2-in-Zinc-Plated-Pan-Head-Phillips-Drive-Sheet-Metal-Screw-50-Piece-801632/204275094) | Home Depot | #8 x 2 in. Zinc-Plated Pan-Head Phillips Drive Sheet Metal Screw (50-Piece) | 1 | 3.51 | 3.51
TOTAL COMPONENTS |  |  | 50 | 857.37 | 857.37

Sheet: Motherboard USA
Item Name | Distributor | Distributor's Item Name | Units | Cost per Unit ($) | Item Cost
POWER
Power Strip (http://www.amazon.com/CyberPower-CSB606-Protector-6-Outlets-Joules/dp/B00FLTTGYG) | AmazonPrime | CyberPower CSB606 Surge Protector 6-Outlets 6-Ft Cord 900 Joules | 1 | 10.15 | 10.15
Main Power Supply (http://www.amazon.com/Switching-Power-Supply-Strip-Light/dp/B007MWNF5Q) | AmazonPrime | 12V 30A 360W Switching Power Supply for LED Strip Light | 1 | 24.96 | 24.96
AC Extension Cable (http://www.amazon.com/gp/product/B0002J1KS0/ref=ox_sc_act_title_1?ie=UTF8&psc=1&smid=ATVPDKIKX0DER) | AmazonPrime | C2G / Cables To Go 03137 18 AWG Outlet Saver Power Extension Cord for NEMA 5-15P to NEMA 5-15R, Black (1 Foot/0.30 Meters) | 1 | 4.99 | 4.99
BRAINS
Raspberry Pi Power Supply (http://www.amazon.com/CanaKit-Raspberry-Power-Supply-Listed/dp/B00MARDJZ4) | AmazonPrime | CanaKit 5V 2.5A Raspberry Pi 2 Power Supply (UL Listed) | 1 | 9.99 | 9.99
Arduino Mega 2560 (http://www.amazon.com/Ximico-Arduino-Cable-Atmega2560-16au-Compatible/dp/B00KG3SBE8?s=pc) | AmazonPrime | Ximico Mega 2560 R3 for Arduino + USB Cable / Mega 2560 R3 Atmega2560-16au Board (Compatible with Arduino) | 1 | 14.19 | 14.19
Raspberry Pi 2 Model B (http://www.amazon.com/Raspberry-Pi-Model-Desktop-Linux/dp/B00T2U7R7I) | AmazonPrime | Raspberry Pi 2 Model B Desktop (Quad Core CPU 900 MHz, 1 GB RAM, Linux) | 1 | 41.87 | 41.87
Micro SD Card (http://www.amazon.com/Kingston-microSDHC-Memory-SDC4-8GBET/dp/B00200K1TS?s=pc) | AmazonPrime | Kingston 8 GB microSDHC Class 4 Flash Memory Card SDC4/8GBET | 1 | 3.99 | 3.99
Ethernet cable (http://www.amazon.com/gp/product/B00EUHRLF6) | AmazonPrime |  | 1 | 5.99 | 5.99
Arduino Mega Protoshield (http://www.amazon.com/Gikfun-Protoshield-Prototype-Shield-Arduino/dp/B00Q9YBQ04?s=pc) | AmazonPrime | Gikfun Protoshield Prototype Shield DIY KIT A1 for Arduino Mega 1280 2560 R1 - R3 | 1 | 8.99 | 8.99
Grove Base Shield (http://www.seeedstudio.com/depot/Base-Shield-V2-p-1378.html) | SeeedStudio | Base Shield V2 | 1 | 8.9 | 8.9
Touchscreen Display (https://www.adafruit.com/products/2097) | Adafruit | PiTFT - Assembled 480x320 3.5" TFT+Touchscreen for Raspberry Pi | 1 | 44.95 | 44.95
GPIO Cable (http://www.amazon.com/ribbon-cable-Raspberry-stackable-header/dp/B00G84WNA2) | AmazonPrime | GPIO ribbon cable for Raspberry Pi set with 2x13 stackable header and 2x13 box header | 1 | 3.99 | 3.99
VOLTAGE CONTROL
4-Channel Relay (http://www.amazon.com/JBtek-Channel-Module-Arduino-Raspberry/dp/B00KTEN3TM?s=pc) | AmazonPrime | JBtek 4 Channel DC 5V Relay Module for Arduino Raspberry Pi DSP AVR PIC ARM | 2 | 6.98 | 13.96
AC Relay Box Back Receptacle (http://www.amazon.com/52171-4E-Pre-Galvanized-Eccentric-Knockouts/dp/B000HEFCKC) | AmazonPrime | Steel City 52171 1/2&3/4E Pre-Galvanized Steel Square Box with Ground Bump and 1/2-Inch and 3/4-Inch Eccentric Knockouts | 1 | 2.04 | 2.04
AC Relay Box Front Panel (http://www.amazon.com/RS8-Outlet-Surface-Square-Galvanized/dp/B000HEIU9W) | AmazonPrime | Steel City RS8 Outlet Box Surface Cover, Square, Raised, 4-Inch, Galvanized | 1 | 4.92 | 4.92
AC Plug (http://www.amazon.com/Leviton-T5320-W-Resistant-Receptacle-Residential/dp/B0015R9M2Y) | AmazonPrime | Leviton T5320-W 15 Amp, 125 Volt, Tamper Resistant, Duplex Receptacle, Residential Grade, Grounding, White | 2 | 1.19 | 2.38
AC Extension Cable (http://www.amazon.com/gp/product/B0002J1KS0/ref=ox_sc_act_title_1?ie=UTF8&psc=1&smid=ATVPDKIKX0DER) | AmazonPrime | C2G / Cables To Go 03137 18 AWG Outlet Saver Power Extension Cord for NEMA 5-15P to NEMA 5-15R, Black (1 Foot/0.30 Meters) | 1 | 4.99 | 4.99
LIGHTS
White LED Strip (http://www.amazon.com/Triangle-Bulbs-T93007-Waterproof-Flexible/dp/B005EHHLD8) | AmazonPrime | Triangle Bulbs T93007 - Waterproof Flexible LED Strip Light, 300 LED's, 3528 SMD, Pure White, 16.4 feet / 5M | 2 | 9.99 | 19.98
Grow LED Panel (http://www.amazon.com/Erligpowht-Indoor-Garden-Plant-Hanging/dp/B00S2DPYQM) | AmazonPrime | Erligpowht 45W LED Red Blue Indoor Garden Plant Grow Light Hanging Light | 2 | 37.99 | 75.98
AIR CONDITIONING
Heater (http://www.amazon.com/dp/B003XDTWN2/ref=sr_ph?&ie=UTF8&qid=1440085101&sr=1&keywords=heater) | AmazonPrime | Lasko #100 MyHeat Personal Ceramic Heater | 1 | 15.99 | 15.99
Humidifier (http://www.amazon.com/Acoustic-Audio-Tek%C2%A8Portable-Humidifier-travel--White/dp/B00RM5Z44S?s=home-garden) | AmazonPrime | Acoustic Audio Tek¨Portable Bottle Cap Air Humidifier with bottle for office home travel--White | 1 | 7.35 | 7.35
USB Wall Adapter (http://www.amazon.com/dp/B00WJW3NM4/ref=twister_B00WJW3M3Y?_encoding=UTF8&psc=1) | AmazonPrime | 3 Pcs High Quality USB Ac Universal Power Home Wall Travel Charger Adapter | 1 | 7.99 | 7.99
Circulation/Vent Fans (http://www.amazon.com/Bgears-b-Blaster-120mm-Bearing-Extreme/dp/B0043GKY1W) | AmazonPrime | Bgears b-Blaster 120mm 2 Ball Bearing High Speed Extreme Airflow Fan | 2 | 12.93 | 25.86
Fan Guards (http://www.amazon.com/Tjernlund-1519003-Wire-Fan-Guard/dp/B008RMKFTO) | AmazonPrime | Tjernlund 1519003 Wire Fan Guard, 120 mm | 2 | 2 | 4
Fan Louvres (http://www.amazon.com/Dundas-Jafine-LC4WZW-ProVent-4-Inches/dp/B0016487CC) | AmazonPrime | Dundas Jafine LC4WZW ProVent White Exhaust Cap, 4-Inches | 2 | 6.84 | 13.68
ENVIRONMENTAL SENSING
CO2 Sensor (http://www.co2meter.com/products/cozir-0-2-co2-sensor) | CO2Meter.com | COZIR Ambient 5K CO2 Sensor | 1 | 109 | 109
Air Temperature and Humidity Sensor (http://www.seeedstudio.com/depot/Grove-TemperatureHumidity-Sensor-Pro-p-838.html) | SeeedStudio | Grove - Temperature&Humidity Sensor Pro | 1 | 14.9 | 14.9
Light Intensity Sensor (http://www.seeedstudio.com/depot/Grove-Digital-Light-Sensor-p-1281.html) | SeeedStudio | Grove - Digital Light Sensor | 1 | 9.9 | 9.9
Webcam (http://www.amazon.com/gp/product/B00YCDHQ8K?psc=1&redirect=true&ref_=oh_aui_detailpage_o06_s00) | AmazonPrime | ELP 2.1mm Lens Wide Angle Webcam Low Illumination USB Camera Module for Day&night Linux Vision | 1 | 39.9 | 39.9
ENCLOSURE SENSING
Magnetic Switch (http://www.amazon.com/gp/product/B0009SUF08?keywords=reed%20switch&qid=1443805349&ref_=sr_1_1&sr=8-1) | AmazonPrime | Magnetic Switch | 1 | 7.2 | 7.2
Limit Switch (http://www.amazon.com/Micro-Limit-Switch-Roller-Action/dp/B00E0JOTV8?s=lamps-light) | Amazon | 10 Pcs Mini Micro Limit Switch Roller Lever Arm SPDT Snap Action LOT | 1 | 3.4 | 3.4
WATER CONDITIONING
Air Pump (http://www.amazon.com/gp/product/B0009YJ4N6?redirect=true) | AmazonPrime | Tetra Whisper Air Pump (Non-UL) | 1 | 9.38 | 9.38
Air Stone (http://www.amazon.com/Jardin-Aquarium-Ceramic-Diffusers-Diameter/dp/B0050HJ7Q6/ref=pd_bxgy_199_img_z) | AmazonPrime | Jardin Aquarium Fish Tank Ponds Ceramic Air Stone Diffusers, 40mm Diameter | 1 | 3.11 | 3.11
Air Pump Tubing (http://www.amazon.com/Standard-Airline-Tubing-Accessories-25-Feet/dp/B0002563MW) | AmazonPrime | Penn-Plax® Flexible Air Line Tubing for Aquariums | 1 | 4.04 | 4.04
Aquarium Pump (http://www.amazon.com/gp/product/B00EWENMAU?redirect=true) | Amazon Prime | VicTsing 80 GPH Submersible Hydroponics Aquaponics Statuary Water Fountain Pump | 1 | 7.99 | 7.99
Pump Tubing (http://www.amazon.com/gp/product/B0079QUTSQ?redirect=true) | Amazon Prime | Hydrofarm HGTB50GF 1/2-Inch Black Tubing, 25 foot Roll | 1 | 14.39 | 14.39
WATER SENSING
Water Temperature and EC Sensor (http://www.dfrobot.com/index.php?route=product/product&product_id=1123&search=DFR0300#.VdTDoFNViko) | DFRobot | Analog Electrical Conductivity Meter (With Temperature Compensation) | 1 | 69.9 | 69.9
pH Sensor (http://www.dfrobot.com/index.php?route=product/product&product_id=1025#.Vg60SBNViko) | DFRobot | Analog pH Meter Kit | 1 | 29.5 | 29.5
ENCLOSURES
Cable Management Box (http://www.amazon.com/gp/product/B00BL63ZU4?psc=1&redirect=true&ref_=oh_aui_detailpage_o01_s00) | AmazonPrime | ORICO PB3218 Power Strip Cord Management Box Cable Box Cable Storage Box (Black) | 1 | 19.99 | 19.99
ADDITIONAL COMPONENTS
Sacrificial AC Extension Cable for high gauge wire | AmazonPrime | C2G / Cables To Go 53408 18 AWG Outlet Saver Power Extension Cord for NEMA 5-15P to NEMA 5-15R, Black (12 Feet/3.65 Meters) | 1 | 10.93 | 10.93
Wago Lever Nut Assortment (http://www.amazon.com/Wago-222-412-222-413-Lever-Nut-Assortment/dp/B00U4520JK) | AmazonPrime | Wago (25) 222-412 (25) 222-413 (20) 222-415 Lever-Nut Assortment Pack | 1 | 39.99 | 39.99
Heat Shrink Tubing (http://www.amazon.com/Vktech-150pcs-Shrink-Tubing-Sleeving/dp/B00EXLPLTW) | AmazonPrime | Vktech 150pcs 2:1 Heat Shrink Tubing Tube Sleeving Wire Cable 8 Sizes 2-13mm Black | 1 | 6.2 | 6.2
Grove Cables (http://www.seeedstudio.com/depot/Grove-c-98_106_57/?ref=crumb) | SeeedStudio | Buy an assortment of 10-50cm grove cables for this build. The 50cm cables
 |  | are better for the sensors and the shorter cables can be used as needed.
Foam mounting tape (http://www.homedepot.com/p/3M-Scotch-1-in-x-12-5-yds-Indoor-Outdoor-Mounting-Tape-411-LONG-DC/100153200) | Home Depot | Foam Mounting Tape | 1 | 15.97 | 15.97
Electrical Tape (http://www.amazon.com/3M-Electrical-75-Inch-66-Foot-0085-Inch/dp/B00004WCCP?s=industrial) | Amazon | Electrical Tape | 1 | 3.98 | 3.98
Air Exchange Box (http://www.digikey.com/product-search/en?KeyWords=377-2132-ND&WT.z_header=search_go) | Digikey | Plastic Box | 1 | 29.5 | 29.5
Short Screws (http://www.homedepot.com/p/Everbilt-6-x-1-2-in-Stainless-Steel-Pan-Head-Phillips-Sheet-Metal-Screw-50-per-Pack-800162/204275035) | Home Depot | #6 x 1/2 in. Stainless Steel Pan-Head Phillips Sheet Metal Screw (50 per Pack) | 1 | 5.8 | 5.8
Long Screws (http://www.homedepot.com/p/Everbilt-8-x-2-in-Zinc-Plated-Pan-Head-Phillips-Drive-Sheet-Metal-Screw-50-Piece-801632/204275094) | Home Depot | #8 x 2 in. Zinc-Plated Pan-Head Phillips Drive Sheet Metal Screw (50-Piece) | 1 | 3.51 | 3.51
TOTAL COMPONENTS |  |  | 54 | 840.56 | 840.56
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

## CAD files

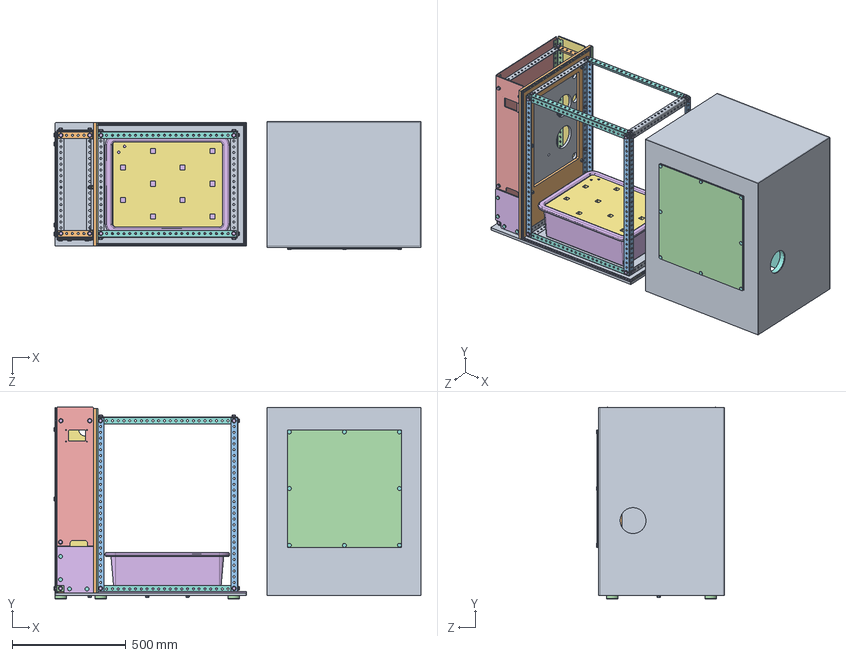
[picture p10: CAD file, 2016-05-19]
Hardware/Food Computer CAD/Food Computer Assembly.SLDASM
1612.9 x 843.5 x 562.0 mm
base board
foot pad x 6
hex bolt 3-8 1L x 26
foot x 6
washer 3-8 x 62
weatherstrip base horiz x 2
weatherstrip depth x 2
punched angle 24L x 4
punched angle 18L x 7
punched angle 6L x 4
punched angle 30L x 4
punched angle 30 1-2L x 2
punched angle bracket x 2
hex bolt 3-8 1-2L x 36
hex nut 3-8 x 65
disc magnet x 44
motherboard panel
motherboard dock panel
hex bolt 3-8 1 1-2L x 6
weatherstrip motherboard vert x 2
upper front plate
lower front plate
back plate
foam box
plastic box
weatherstrip window horiz x 4
weatherstrip window vert x 4
window
side plate
reservoir bin
plant tray

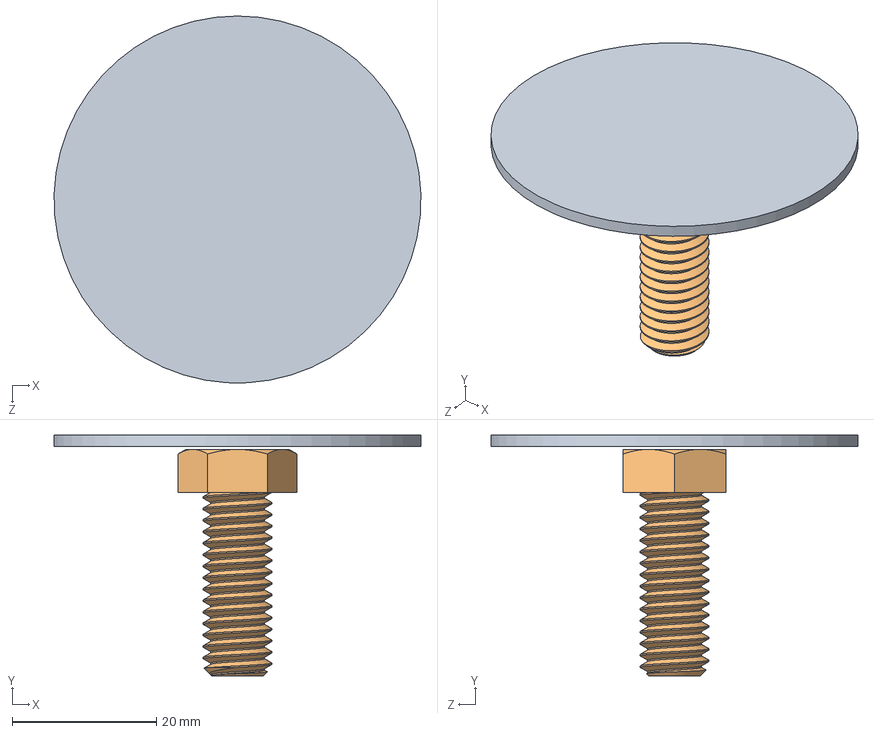
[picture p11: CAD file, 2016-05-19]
Hardware/Food Computer CAD/SUBASSEMBLIES/Foot SubAssem.SLDASM
50.8 x 33.3 x 50.8 mm
foot pad
hex bolt 3-8 1L

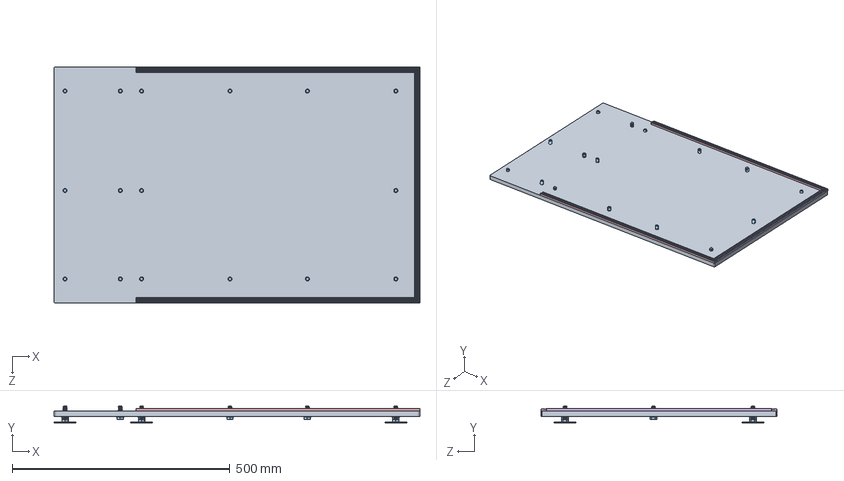
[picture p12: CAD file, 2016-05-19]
Hardware/Food Computer CAD/SUBASSEMBLIES/Base SubAssem.SLDASM
841.1 x 38.7 x 542.9 mm
base board
foot pad x 6
hex bolt 3-8 1L x 16
washer 3-8 x 10
weatherstrip base horiz x 2
weatherstrip depth

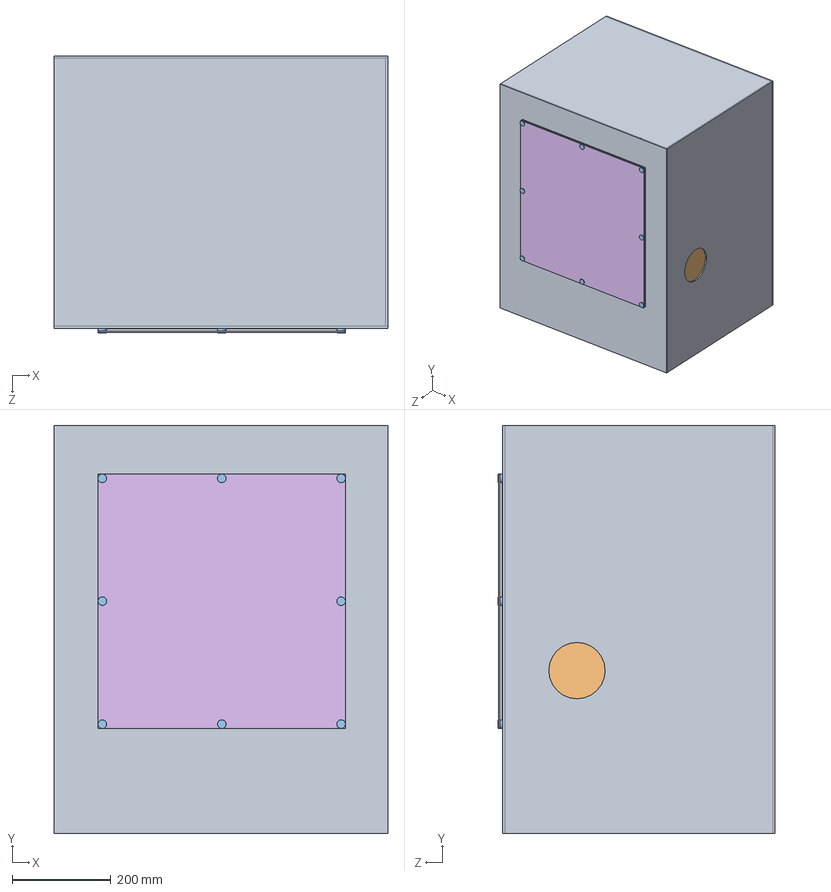
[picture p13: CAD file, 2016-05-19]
Hardware/Food Computer CAD/SUBASSEMBLIES/Jacket SubAssem.SLDASM
676.3 x 827.1 x 562.0 mm
foam box
plastic box
disc magnet x 24
weatherstrip window horiz x 4
weatherstrip window vert x 4
window

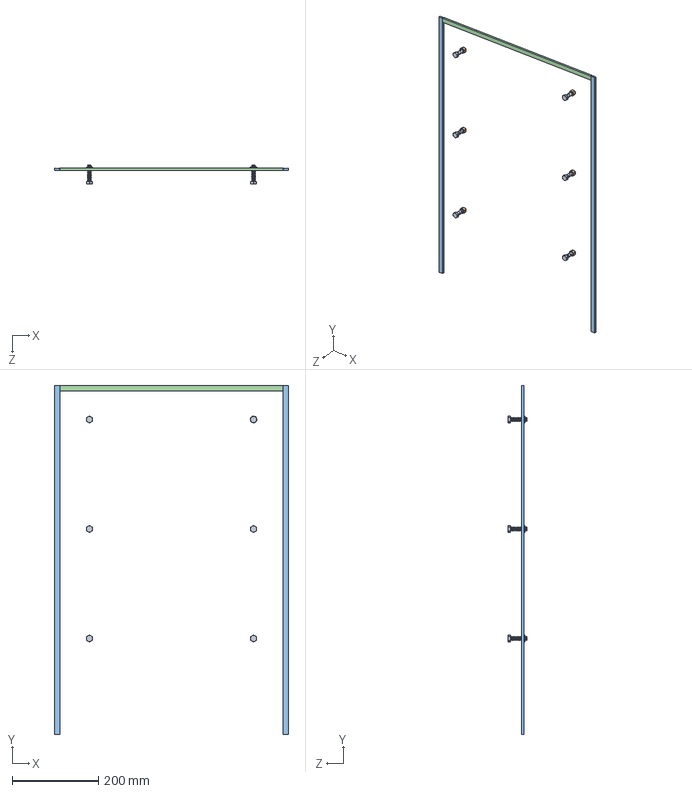
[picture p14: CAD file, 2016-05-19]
Hardware/Food Computer CAD/SUBASSEMBLIES/Motherboard SubAssem.SLDASM
542.9 x 809.6 x 44.1 mm
hex bolt 3-8 1 1-2L x 6
hex nut 3-8 x 6
weatherstrip motherboard vert x 2
weatherstrip depth

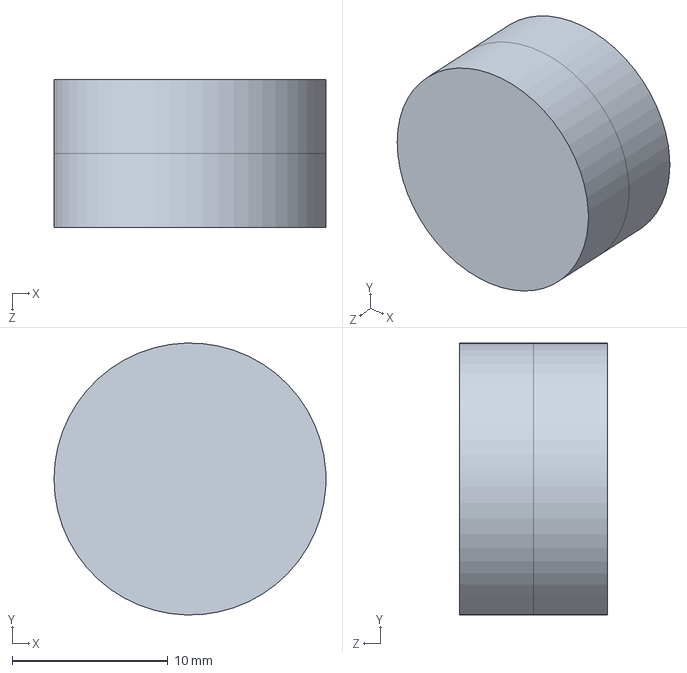
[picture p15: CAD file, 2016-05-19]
Hardware/Food Computer CAD/SUBASSEMBLIES/Double magnet SubAssem.SLDASM
17.5 x 17.5 x 9.52 mm
disc magnet x 2

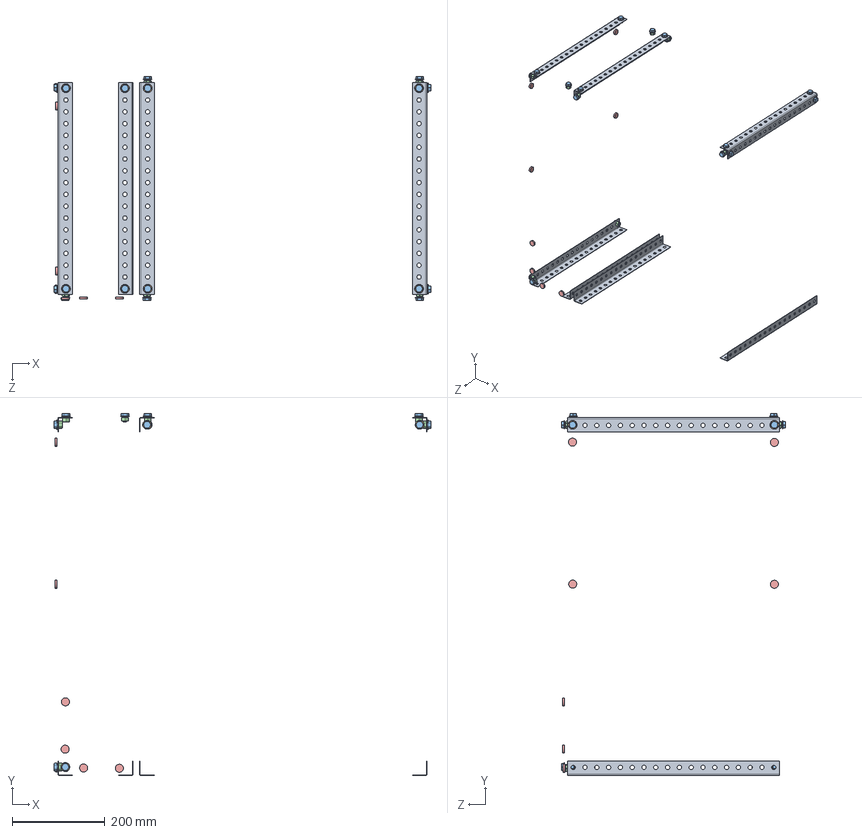
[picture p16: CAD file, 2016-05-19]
Hardware/Food Computer CAD/SUBASSEMBLIES/Metal Frame SubAssem.SLDASM
811.5 x 779.4 x 483.2 mm
punched angle 18L x 7
washer 3-8 x 19
hex bolt 3-8 1-2L x 19
hex nut 3-8 x 19
disc magnet x 10

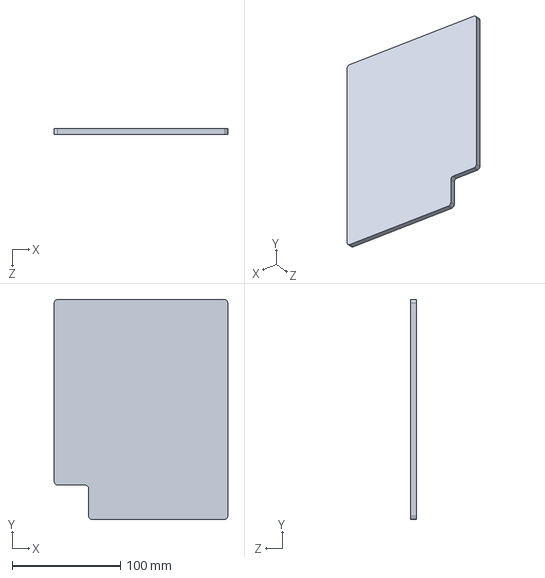
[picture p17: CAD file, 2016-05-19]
Hardware/Food Computer CAD/PARTS/ACRYLIC/lower front plate/lower front plate.SLDPRT
160.3 x 203.2 x 5.59 mm

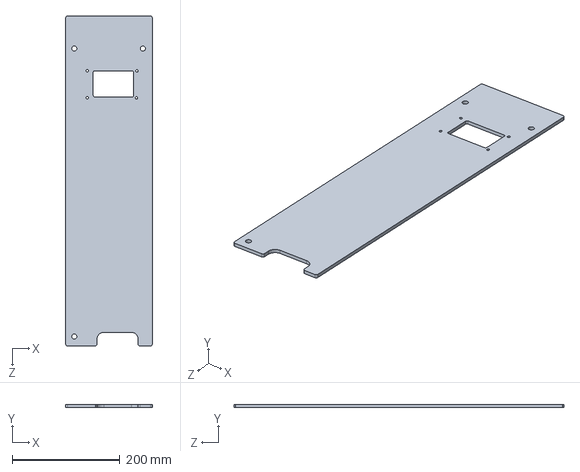
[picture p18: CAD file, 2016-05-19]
Hardware/Food Computer CAD/PARTS/ACRYLIC/upper front plate/upper front plate.SLDPRT
160.3 x 5.59 x 611.2 mm

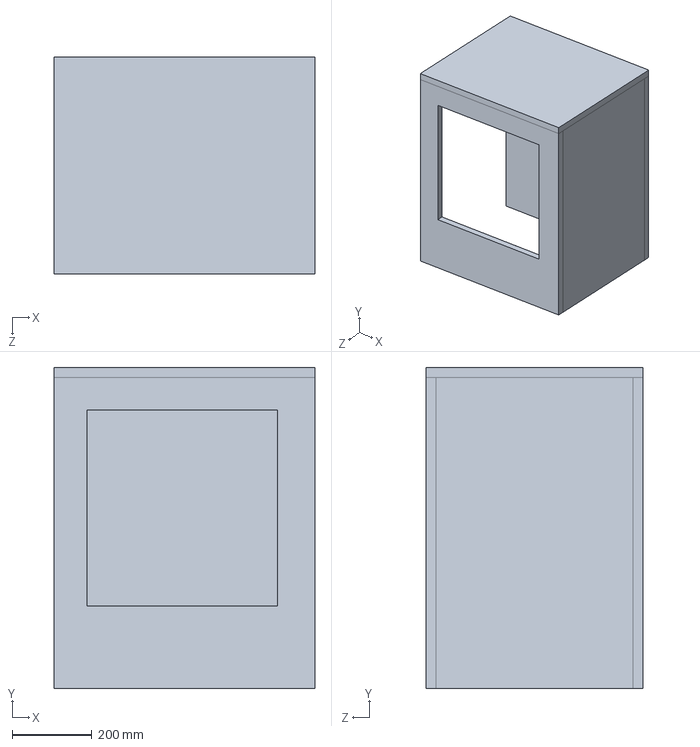
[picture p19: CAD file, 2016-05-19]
Hardware/Food Computer CAD/PARTS/foam box/foam box.SLDPRT
652.5 x 803.3 x 542.9 mm

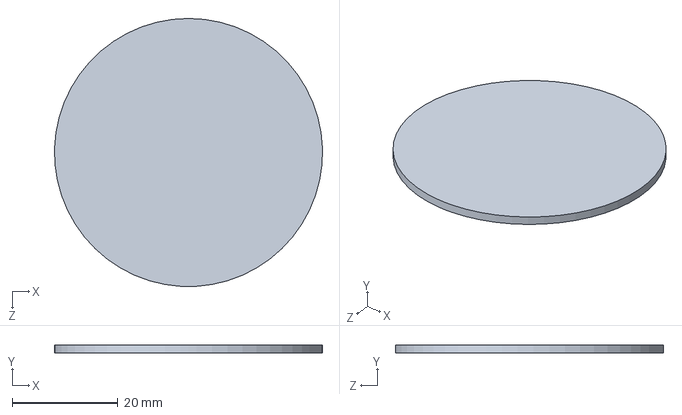
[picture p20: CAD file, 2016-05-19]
Hardware/Food Computer CAD/PARTS/foot pad/foot pad.SLDPRT
50.8 x 1.59 x 50.8 mm

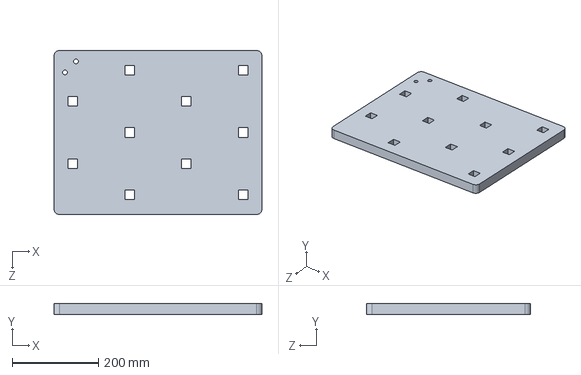
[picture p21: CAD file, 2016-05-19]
Hardware/Food Computer CAD/PARTS/plant tray/plant tray.SLDPRT
481.0 x 25.4 x 379.4 mm

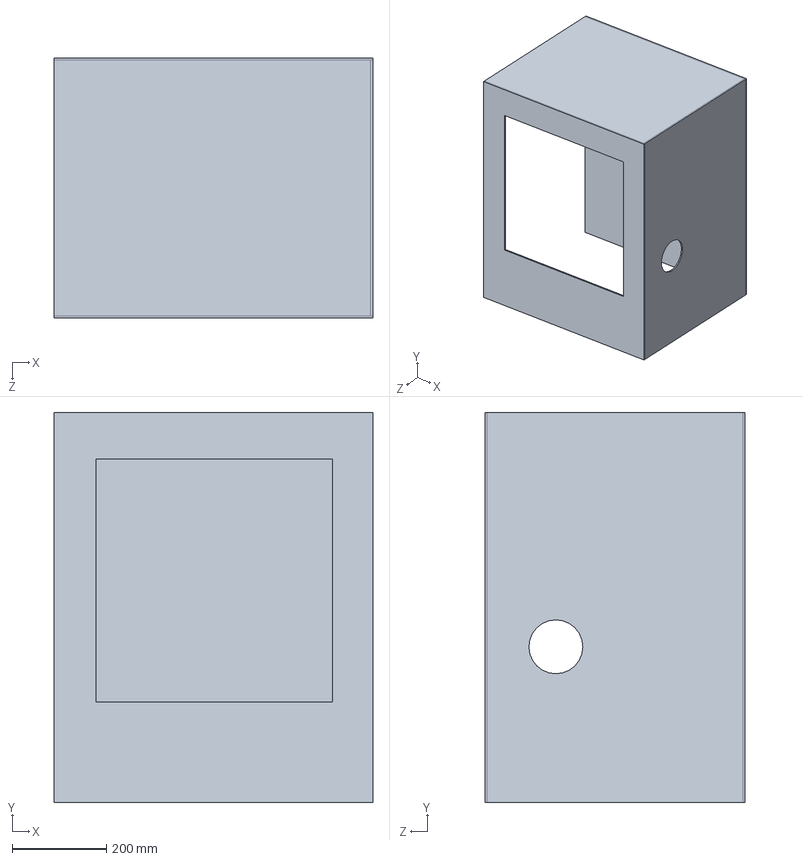
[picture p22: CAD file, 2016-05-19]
Hardware/Food Computer CAD/PARTS/plastic box/plastic box.SLDPRT
676.3 x 827.1 x 552.4 mm

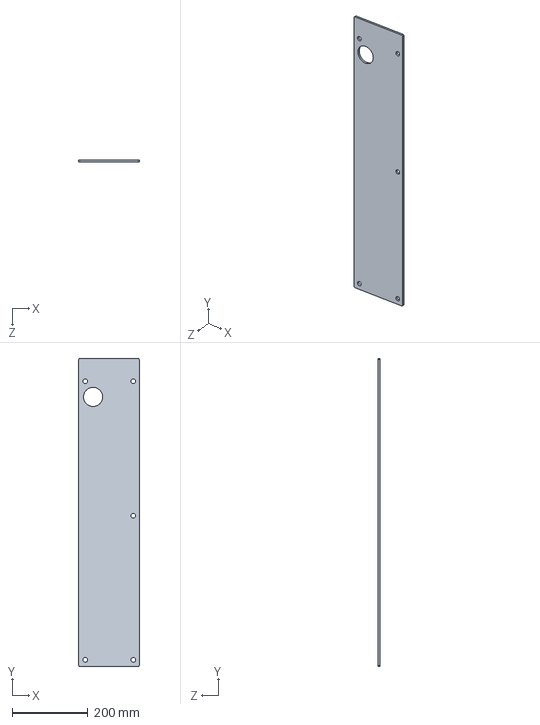
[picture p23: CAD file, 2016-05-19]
Hardware/Food Computer CAD/PARTS/POLYCARBONATE/back plate/back plate.SLDPRT
160.3 x 814.4 x 5.59 mm

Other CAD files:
Hardware/Food Computer basic P&ID.dwg
Hardware/Food Computer CAD/PARTS/POLYCARBONATE/side plate/side plate.SLDPRT
Hardware/Food Computer CAD/PARTS/POLYCARBONATE/window/window.SLDPRT
Hardware/Food Computer CAD/PARTS/PUNCHED ANGLE/punched angle 18L/punched angle 18L.SLDPRT
Hardware/Food Computer CAD/PARTS/FASTENERS/disc magnet/disc magnet.SLDPRT
Hardware/Food Computer CAD/PARTS/FASTENERS/hex bolt 3-8 1 1-2L/hex bolt 3-8 1 1-2L.SLDPRT
Hardware/Food Computer CAD/PARTS/FASTENERS/hex bolt 3-8 1-2L/hex bolt 3-8 1-2L.SLDPRT
Hardware/Food Computer CAD/PARTS/FASTENERS/hex bolt 3-8 1L/hex bolt 3-8 1L.SLDPRT
Hardware/Food Computer CAD/PARTS/FASTENERS/hex nut 3-8/hex nut 3-8.SLDPRT
Hardware/Food Computer CAD/PARTS/FASTENERS/washer 3-8/washer 3-8.SLDPRT
Hardware/Food Computer CAD/PARTS/PUNCHED ANGLE/punched angle 24L/punched angle 24L.SLDPRT
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

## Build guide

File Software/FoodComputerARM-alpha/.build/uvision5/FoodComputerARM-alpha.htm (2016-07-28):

# Static Call Graph for image .\.build\uvision5\FoodComputerARM-alpha.axf

#<CALLGRAPH># ARM Linker, 5060183: Last Updated: Thu Jul 28 17:25:11 2016

### Maximum Stack Usage = 832 bytes + Unknown(Cycles, Untraceable Function Pointers)

### Call chain for Maximum Stack Depth:

update_modbus() ⇒ ModbusSlave232::update(int*, unsigned) ⇒ ModbusSlave232::read_holding_registers(unsigned, unsigned char, int*) ⇒ mbed::Stream::putc(int) ⇒ fflush ⇒ _do_fflush ⇒ _fflush ⇒ _writebuf ⇒ _sys_write ⇒ serial_init ⇒ mbed_assert_internal (Cycle)

### Mutually Recursive functions

- NMI_Handler ⇒ NMI_Handler
- HardFault_Handler ⇒ HardFault_Handler
- MemManage_Handler ⇒ MemManage_Handler
- BusFault_Handler ⇒ BusFault_Handler
- UsageFault_Handler ⇒ UsageFault_Handler
- SVC_Handler ⇒ SVC_Handler
- DebugMon_Handler ⇒ DebugMon_Handler
- PendSV_Handler ⇒ PendSV_Handler
- SysTick_Handler ⇒ SysTick_Handler
- ADC_IRQHandler ⇒ ADC_IRQHandler
- pin_mode ⇒ mbed_assert_internal
- Set_GPIO_Clock ⇒ error
- gpio_init_out ⇒ mbed_assert_internal
- gpio_dir ⇒ mbed_assert_internal
- pin_function ⇒ mbed_assert_internal
- mbed_die ⇒ mbed_assert_internal
- serial_init ⇒ mbed_assert_internal
- pinmap_merge ⇒ error
- pinmap_pinout ⇒ error
- pinmap_peripheral ⇒ error
- SoftSerial::_getc() ⇒ SoftSerial::_getc()

### Function Pointers

- ⟨Func1⟩ from SerialBase.o(i.) referenced from SerialBase.o(i._ZN4mbed10SerialBaseC1E7PinNameS1_)
- ⟨Func4⟩ from softserial.o(i.) referenced from softserial.o(i._ZN10SoftSerialC1E7PinNameS0_PKc)
- ADC_IRQHandler from startup_stm32f401xe.o(.text) referenced from startup_stm32f401xe.o(RESET)
- BusFault_Handler from startup_stm32f401xe.o(.text) referenced from startup_stm32f401xe.o(RESET)
- DMA1_Stream0_IRQHandler from startup_stm32f401xe.o(.text) referenced from startup_stm32f401xe.o(RESET)
- DMA1_Stream1_IRQHandler from startup_stm32f401xe.o(.text) referenced from startup_stm32f401xe.o(RESET)
- DMA1_Stream2_IRQHandler from startup_stm32f401xe.o(.text) referenced from startup_stm32f401xe.o(RESET)
- DMA1_Stream3_IRQHandler from startup_stm32f401xe.o(.text) referenced from startup_stm32f401xe.o(RESET)
- DMA1_Stream4_IRQHandler from startup_stm32f401xe.o(.text) referenced from startup_stm32f401xe.o(RESET)
- DMA1_Stream5_IRQHandler from startup_stm32f401xe.o(.text) referenced from startup_stm32f401xe.o(RESET)
- DMA1_Stream6_IRQHandler from startup_stm32f401xe.o(.text) referenced from startup_stm32f401xe.o(RESET)
- DMA1_Stream7_IRQHandler from startup_stm32f401xe.o(.text) referenced from startup_stm32f401xe.o(RESET)
- DMA2_Stream0_IRQHandler from startup_stm32f401xe.o(.text) referenced from startup_stm32f401xe.o(RESET)
- DMA2_Stream1_IRQHandler from startup_stm32f401xe.o(.text) referenced from startup_stm32f401xe.o(RESET)
- DMA2_Stream2_IRQHandler from startup_stm32f401xe.o(.text) referenced from startup_stm32f401xe.o(RESET)
- DMA2_Stream3_IRQHandler from startup_stm32f401xe.o(.text) referenced from startup_stm32f401xe.o(RESET)
- DMA2_Stream4_IRQHandler from startup_stm32f401xe.o(.text) referenced from startup_stm32f401xe.o(RESET)
- DMA2_Stream5_IRQHandler from startup_stm32f401xe.o(.text) referenced from startup_stm32f401xe.o(RESET)
- DMA2_Stream6_IRQHandler from startup_stm32f401xe.o(.text) referenced from startup_stm32f401xe.o(RESET)
- DMA2_Stream7_IRQHandler from startup_stm32f401xe.o(.text) referenced from startup_stm32f401xe.o(RESET)
- DebugMon_Handler from startup_stm32f401xe.o(.text) referenced from startup_stm32f401xe.o(RESET)
- EXTI0_IRQHandler from startup_stm32f401xe.o(.text) referenced from startup_stm32f401xe.o(RESET)
- EXTI15_10_IRQHandler from startup_stm32f401xe.o(.text) referenced from startup_stm32f401xe.o(RESET)
- EXTI1_IRQHandler from startup_stm32f401xe.o(.text) referenced from startup_stm32f401xe.o(RESET)
- EXTI2_IRQHandler from startup_stm32f401xe.o(.text) referenced from startup_stm32f401xe.o(RESET)
- EXTI3_IRQHandler from startup_stm32f401xe.o(.text) referenced from startup_stm32f401xe.o(RESET)
- EXTI4_IRQHandler from startup_stm32f401xe.o(.text) referenced from startup_stm32f401xe.o(RESET)
- EXTI9_5_IRQHandler from startup_stm32f401xe.o(.text) referenced from startup_stm32f401xe.o(RESET)
- FLASH_IRQHandler from startup_stm32f401xe.o(.text) referenced from startup_stm32f401xe.o(RESET)
- FPU_IRQHandler from startup_stm32f401xe.o(.text) referenced from startup_stm32f401xe.o(RESET)
- HardFault_Handler from startup_stm32f401xe.o(.text) referenced from startup_stm32f401xe.o(RESET)
- I2C1_ER_IRQHandler from startup_stm32f401xe.o(.text) referenced from startup_stm32f401xe.o(RESET)
- I2C1_EV_IRQHandler from startup_stm32f401xe.o(.text) referenced from startup_stm32f401xe.o(RESET)
- I2C2_ER_IRQHandler from startup_stm32f401xe.o(.text) referenced from startup_stm32f401xe.o(RESET)
- I2C2_EV_IRQHandler from startup_stm32f401xe.o(.text) referenced from startup_stm32f401xe.o(RESET)
- I2C3_ER_IRQHandler from startup_stm32f401xe.o(.text) referenced from startup_stm32f401xe.o(RESET)
- I2C3_EV_IRQHandler from startup_stm32f401xe.o(.text) referenced from startup_stm32f401xe.o(RESET)
- MemManage_Handler from startup_stm32f401xe.o(.text) referenced from startup_stm32f401xe.o(RESET)
- NMI_Handler from startup_stm32f401xe.o(.text) referenced from startup_stm32f401xe.o(RESET)
- OTG_FS_IRQHandler from startup_stm32f401xe.o(.text) referenced from startup_stm32f401xe.o(RESET)
- OTG_FS_WKUP_IRQHandler from startup_stm32f401xe.o(.text) referenced from startup_stm32f401xe.o(RESET)
- PVD_IRQHandler from startup_stm32f401xe.o(.text) referenced from startup_stm32f401xe.o(RESET)
- PendSV_Handler from startup_stm32f401xe.o(.text) referenced from startup_stm32f401xe.o(RESET)
- RCC_IRQHandler from startup_stm32f401xe.o(.text) referenced from startup_stm32f401xe.o(RESET)
- RTC_Alarm_IRQHandler from startup_stm32f401xe.o(.text) referenced from startup_stm32f401xe.o(RESET)
- RTC_WKUP_IRQHandler from startup_stm32f401xe.o(.text) referenced from startup_stm32f401xe.o(RESET)
- Reset_Handler from startup_stm32f401xe.o(.text) referenced from startup_stm32f401xe.o(RESET)
- SDIO_IRQHandler from startup_stm32f401xe.o(.text) referenced from startup_stm32f401xe.o(RESET)
- SPI1_IRQHandler from startup_stm32f401xe.o(.text) referenced from startup_stm32f401xe.o(RESET)
- SPI2_IRQHandler from startup_stm32f401xe.o(.text) referenced from startup_stm32f401xe.o(RESET)
- SPI3_IRQHandler from startup_stm32f401xe.o(.text) referenced from startup_stm32f401xe.o(RESET)
- SPI4_IRQHandler from startup_stm32f401xe.o(.text) referenced from startup_stm32f401xe.o(RESET)
- SVC_Handler from startup_stm32f401xe.o(.text) referenced from startup_stm32f401xe.o(RESET)
- SysTick_Handler from startup_stm32f401xe.o(.text) referenced from startup_stm32f401xe.o(RESET)
- SystemInit from system_stm32f4xx.o(i.SystemInit) referenced from startup_stm32f401xe.o(.text)
- TAMP_STAMP_IRQHandler from startup_stm32f401xe.o(.text) referenced from startup_stm32f401xe.o(RESET)
- TIM1_BRK_TIM9_IRQHandler from startup_stm32f401xe.o(.text) referenced from startup_stm32f401xe.o(RESET)
- TIM1_CC_IRQHandler from startup_stm32f401xe.o(.text) referenced from startup_stm32f401xe.o(RESET)
- TIM1_TRG_COM_TIM11_IRQHandler from startup_stm32f401xe.o(.text) referenced from startup_stm32f401xe.o(RESET)
- TIM1_UP_TIM10_IRQHandler from startup_stm32f401xe.o(.text) referenced from startup_stm32f401xe.o(RESET)
- TIM2_IRQHandler from startup_stm32f401xe.o(.text) referenced from startup_stm32f401xe.o(RESET)
- TIM3_IRQHandler from startup_stm32f401xe.o(.text) referenced from startup_stm32f401xe.o(RESET)
- TIM4_IRQHandler from startup_stm32f401xe.o(.text) referenced from startup_stm32f401xe.o(RESET)
- TIM5_IRQHandler from startup_stm32f401xe.o(.text) referenced from startup_stm32f401xe.o(RESET)
- USART1_IRQHandler from startup_stm32f401xe.o(.text) referenced from startup_stm32f401xe.o(RESET)
- USART2_IRQHandler from startup_stm32f401xe.o(.text) referenced from startup_stm32f401xe.o(RESET)
- USART6_IRQHandler from startup_stm32f401xe.o(.text) referenced from startup_stm32f401xe.o(RESET)
- UsageFault_Handler from startup_stm32f401xe.o(.text) referenced from startup_stm32f401xe.o(RESET)
- WWDG_IRQHandler from startup_stm32f401xe.o(.text) referenced from startup_stm32f401xe.o(RESET)
- millisTicker() from millis.o(i._Z12millisTickerv) referenced from millis.o(i._Z11startMillisv)
- update_modbus() from main.o(i._Z13update_modbusv) referenced from main.o(i.main)
- __default_new_handler() from arm_newhandler_noexceptions.o(.text) referenced from new.o(i._Znwj)
- FlexTicker::handler() from softserial.o(i._ZN10FlexTicker7handlerEv) referenced from softserial.o(.constdata__ZTV10FlexTicker)
- SoftSerial::rx_handler() from softserial_rx.o(i._ZN10SoftSerial10rx_handlerEv) referenced from softserial.o(.constdata)
- SoftSerial::tx_handler() from softserial_tx.o(i._ZN10SoftSerial10tx_handlerEv) referenced from softserial.o(.constdata)
- SoftSerial::rx_gpio_irq_handler() from softserial_rx.o(i._ZN10SoftSerial19rx_gpio_irq_handlerEv) referenced 2 times from softserial.o(.constdata)
- SoftSerial::_getc() from softserial_rx.o(i._ZN10SoftSerial5_getcEv) referenced from softserial.o(.constdata__ZTV10SoftSerial)
- SoftSerial::_putc(int) from softserial_tx.o(i._ZN10SoftSerial5_putcEi) referenced from softserial.o(.constdata__ZTV10SoftSerial)
- SoftSerial::~SoftSerial() from softserial.o(i._ZN10SoftSerialD1Ev) referenced from softserial.o(.constdata__ZTV10SoftSerial)
- SoftSerial::~SoftSerial() from softserial.o(i._ZN10SoftSerialD1Ev) referenced from main.o(i.__sti___8_main_cpp_led1)
- [local to arm_exceptions_c]::__default_terminate_handler() from arm_exceptions_globs.o(.text) referenced from arm_exceptions_globs.o(.text)
- AjK::MODSERIAL_callback::MODSERIAL_callback() from modserial.o(i._ZN3AjK18MODSERIAL_callbackC1Ev) referenced from modserial.o(i._ZN3AjK9MODSERIALC1E7PinNameS1_PKc)
- AjK::MODSERIAL::isr_rx() from isr_rx.o(i._ZN3AjK9MODSERIAL6isr_rxEv) referenced from init.o(.constdata)
- AjK::MODSERIAL::isr_tx() from init.o(i._ZN3AjK9MODSERIAL6isr_txEv) referenced from init.o(.constdata)
- AjK::MODSERIAL::~MODSERIAL() from modserial.o(i._ZN3AjK9MODSERIALD1Ev) referenced from modserial.o(.constdata__ZTVN3AjK9MODSERIALE)
- AjK::MODSERIAL::~MODSERIAL() from modserial.o(i._ZN3AjK9MODSERIALD1Ev) referenced from modbusslave232.o(i.__sti___18_ModbusSlave232_cpp_pc)
- DHT::~DHT() from dht.o(i._ZN3DHTD1Ev) referenced from main.o(i.__sti___8_main_cpp_led1)
- mbed::FileHandle::flen() from retarget.o(i._ZN4mbed10FileHandle4flenEv) referenced from retarget.o(.constdata__ZTVN4mbed10FileHandleE)
- mbed::FileHandle::flen() from retarget.o(i._ZN4mbed10FileHandle4flenEv) referenced from FileLike.o(.constdata__ZTVN4mbed8FileLikeE)
- mbed::FileHandle::~FileHandle__sub_object() from retarget.o(i._ZN4mbed10FileHandleD2Ev) referenced from retarget.o(.constdata__ZTVN4mbed10FileHandleE)
- mbed::SerialBase::_irq_handler(unsigned, SerialIrq) from SerialBase.o(i._ZN4mbed10SerialBase12_irq_handlerEj9SerialIrq) referenced from SerialBase.o(i._ZN4mbed10SerialBaseC1E7PinNameS1_)
- mbed::TimerEvent::irq(unsigned) from TimerEvent.o(i._ZN4mbed10TimerEvent3irqEj) referenced from TimerEvent.o(i._ZN4mbed10TimerEventC2Ev)
- mbed::TimerEvent::~TimerEvent__sub_object() from TimerEvent.o(i._ZN4mbed10TimerEventD2Ev) referenced from TimerEvent.o(.constdata__ZTVN4mbed10TimerEventE)
- mbed::InterruptIn::_irq_handler(unsigned, gpio_irq_event) from InterruptIn.o(i._ZN4mbed11InterruptIn12_irq_handlerEj14gpio_irq_event) referenced from InterruptIn.o(i._ZN4mbed11InterruptInC1E7PinName)
- mbed::InterruptIn::~InterruptIn__deallocating() from InterruptIn.o(i._ZN4mbed11InterruptInD0Ev) referenced from InterruptIn.o(.constdata__ZTVN4mbed11InterruptInE)
- void mbed::FunctionPointerArg1⟨void, void⟩::membercaller⟨SoftSerial⟩(void*, unsigned*) from softserial.o(t._ZN4mbed19FunctionPointerArg1IvvE12membercallerI10SoftSerialEEvPvPj) referenced from softserial_rx.o(i._ZN10SoftSerial10rx_handlerEv)
- void mbed::FunctionPointerArg1⟨void, void⟩::membercaller⟨SoftSerial⟩(void*, unsigned*) from softserial.o(t._ZN4mbed19FunctionPointerArg1IvvE12membercallerI10SoftSerialEEvPvPj) referenced from softserial.o(i._ZN10SoftSerialC1E7PinNameS0_PKc)
- void mbed::FunctionPointerArg1⟨void, void⟩::membercaller⟨AjK::MODSERIAL⟩(void*, unsigned*) from init.o(t._ZN4mbed19FunctionPointerArg1IvvE12membercallerIN3AjK9MODSERIALEEEvPvPj) referenced from init.o(i._ZN3AjK9MODSERIAL4initEii7PinName)
- mbed::Stream::flen() from Stream.o(i._ZN4mbed6Stream4flenEv) referenced from softserial.o(.constdata__ZTV10SoftSerial)
- mbed::Stream::flen() from Stream.o(i._ZN4mbed6Stream4flenEv) referenced from modserial.o(.constdata__ZTVN3AjK9MODSERIALE)
- mbed::Stream::flen() from Stream.o(i._ZN4mbed6Stream4flenEv) referenced from Serial.o(.constdata__ZTVN4mbed6SerialE)
- mbed::Stream::flen() from Stream.o(i._ZN4mbed6Stream4flenEv) referenced from Stream.o(.constdata__ZTVN4mbed6StreamE)
- mbed::Stream::read(void*, unsigned) from Stream.o(i._ZN4mbed6Stream4readEPvj) referenced from softserial.o(.constdata__ZTV10SoftSerial)
- mbed::Stream::read(void*, unsigned) from Stream.o(i._ZN4mbed6Stream4readEPvj) referenced from modserial.o(.constdata__ZTVN3AjK9MODSERIALE)
- mbed::Stream::read(void*, unsigned) from Stream.o(i._ZN4mbed6Stream4readEPvj) referenced from Serial.o(.constdata__ZTVN4mbed6SerialE)
- mbed::Stream::read(void*, unsigned) from Stream.o(i._ZN4mbed6Stream4readEPvj) referenced from Stream.o(.constdata__ZTVN4mbed6StreamE)
- mbed::Stream::close() from Stream.o(i._ZN4mbed6Stream5closeEv) referenced from softserial.o(.constdata__ZTV10SoftSerial)
- mbed::Stream::close() from Stream.o(i._ZN4mbed6Stream5closeEv) referenced from modserial.o(.constdata__ZTVN3AjK9MODSERIALE)
- mbed::Stream::close() from Stream.o(i._ZN4mbed6Stream5closeEv) referenced from Serial.o(.constdata__ZTVN4mbed6SerialE)
- mbed::Stream::close() from Stream.o(i._ZN4mbed6Stream5closeEv) referenced from Stream.o(.constdata__ZTVN4mbed6StreamE)
- mbed::Stream::lseek(long, int) from Stream.o(i._ZN4mbed6Stream5lseekEli) referenced from softserial.o(.constdata__ZTV10SoftSerial)
- mbed::Stream::lseek(long, int) from Stream.o(i._ZN4mbed6Stream5lseekEli) referenced from modserial.o(.constdata__ZTVN3AjK9MODSERIALE)
- mbed::Stream::lseek(long, int) from Stream.o(i._ZN4mbed6Stream5lseekEli) referenced from Serial.o(.constdata__ZTVN4mbed6SerialE)
- mbed::Stream::lseek(long, int) from Stream.o(i._ZN4mbed6Stream5lseekEli) referenced from Stream.o(.constdata__ZTVN4mbed6StreamE)
- mbed::Stream::write(const void*, unsigned) from Stream.o(i._ZN4mbed6Stream5writeEPKvj) referenced from softserial.o(.constdata__ZTV10SoftSerial)
- mbed::Stream::write(const void*, unsigned) from Stream.o(i._ZN4mbed6Stream5writeEPKvj) referenced from modserial.o(.constdata__ZTVN3AjK9MODSERIALE)
- mbed::Stream::write(const void*, unsigned) from Stream.o(i._ZN4mbed6Stream5writeEPKvj) referenced from Serial.o(.constdata__ZTVN4mbed6SerialE)
- mbed::Stream::write(const void*, unsigned) from Stream.o(i._ZN4mbed6Stream5writeEPKvj) referenced from Stream.o(.constdata__ZTVN4mbed6StreamE)
- mbed::Stream::isatty() from Stream.o(i._ZN4mbed6Stream6isattyEv) referenced from softserial.o(.constdata__ZTV10SoftSerial)
- mbed::Stream::isatty() from Stream.o(i._ZN4mbed6Stream6isattyEv) referenced from modserial.o(.constdata__ZTVN3AjK9MODSERIALE)
- mbed::Stream::isatty() from Stream.o(i._ZN4mbed6Stream6isattyEv) referenced from Serial.o(.constdata__ZTVN4mbed6SerialE)
- mbed::Stream::isatty() from Stream.o(i._ZN4mbed6Stream6isattyEv) referenced from Stream.o(.constdata__ZTVN4mbed6StreamE)
- mbed::Stream::~Stream__sub_object() from Stream.o(i._ZN4mbed6StreamD2Ev) referenced from Stream.o(.constdata__ZTVN4mbed6StreamE)
- mbed::Ticker::handler() from Ticker.o(i._ZN4mbed6Ticker7handlerEv) referenced from Ticker.o(.constdata__ZTVN4mbed6TickerE)
- mbed::Ticker::~Ticker() from main.o(i._ZN4mbed6TickerD1Ev) referenced from Ticker.o(.constdata__ZTVN4mbed6TickerE)
- mbed::Ticker::~Ticker() from main.o(i._ZN4mbed6TickerD1Ev) referenced from millis.o(i.__sti___10_millis_cpp_d9fd33a2)
- mbed::Ticker::~Ticker() from main.o(i._ZN4mbed6TickerD1Ev) referenced from main.o(i.__sti___8_main_cpp_led1)
- mbed::FileBase::~FileBase() from FileBase.o(i._ZN4mbed8FileBaseD1Ev) referenced from FileBase.o(.constdata__ZTVN4mbed8FileBaseE)
- mbed::FileLike::~FileLike__sub_object() from FileLike.o(i._ZN4mbed8FileLikeD2Ev) referenced from FileLike.o(.constdata__ZTVN4mbed8FileLikeE)
- thunk{-92} to AjK::MODSERIAL::_getc() from modserial.o(i._ZThn92_N3AjK9MODSERIAL5_getcEv) referenced from modserial.o(.constdata__ZTVN3AjK9MODSERIALE)
- thunk{-92} to AjK::MODSERIAL::_putc(int) from modserial.o(i._ZThn92_N3AjK9MODSERIAL5_putcEi) referenced from modserial.o(.constdata__ZTVN3AjK9MODSERIALE)
- thunk{-92} to mbed::Serial::_getc() from Serial.o(i._ZThn92_N4mbed6Serial5_getcEv) referenced from Serial.o(.constdata__ZTVN4mbed6SerialE)
- thunk{-92} to mbed::Serial::_putc(int) from Serial.o(i._ZThn92_N4mbed6Serial5_putcEi) referenced from Serial.o(.constdata__ZTVN4mbed6SerialE)
- __backspace from backspace.o(.text) referenced from scanf_char_file.o(.text)
- __cxa_pure_virtual from pure_virt.o(i.__cxa_pure_virtual) referenced 6 times from retarget.o(.constdata__ZTVN4mbed10FileHandleE)
- __cxa_pure_virtual from pure_virt.o(i.__cxa_pure_virtual) referenced from TimerEvent.o(.constdata__ZTVN4mbed10TimerEventE)
- __cxa_pure_virtual from pure_virt.o(i.__cxa_pure_virtual) referenced 2 times from Stream.o(.constdata__ZTVN4mbed6StreamE)
- __cxa_pure_virtual from pure_virt.o(i.__cxa_pure_virtual) referenced 6 times from FileLike.o(.constdata__ZTVN4mbed8FileLikeE)
- __main from __main.o(!!!main) referenced from startup_stm32f401xe.o(.text)
- __sti___10_millis_cpp_d9fd33a2 from millis.o(i.__sti___10_millis_cpp_d9fd33a2) referenced from millis.o(.init_array)
- __sti___17_SoftSerial_rx_cpp_a7af12b1 from softserial_rx.o(i.__sti___17_SoftSerial_rx_cpp_a7af12b1) referenced from softserial_rx.o(.init_array)
- __sti___18_ModbusSlave232_cpp_pc from modbusslave232.o(i.__sti___18_ModbusSlave232_cpp_pc) referenced from modbusslave232.o(.init_array)
- __sti___8_main_cpp_led1 from main.o(i.__sti___8_main_cpp_led1) referenced from main.o(.init_array)
- _get_lc_ctype from lc_ctype_c.o(locale$$code) referenced from rt_ctype_table.o(.text)
- _printf_input_char from _printf_char_common.o(.text) referenced from _printf_char_common.o(.text)
- _sbackspace from _sgetc.o(.text) referenced from __0sscanf.o(.text)
- _scanf_char_input from scanf_char.o(.text) referenced from scanf_char.o(.text)
- _sgetc from _sgetc.o(.text) referenced from __0sscanf.o(.text)
- _sputc from _sputc.o(.text) referenced from __2sprintf.o(.text)
- fgetc from fgetc.o(i.fgetc) referenced from scanf_char_file.o(.text)
- fputc from fputc.o(i.fputc) referenced from _printf_char_file.o(.text)
- gpio_irq0 from gpio_irq_api.o(i.gpio_irq0) referenced from gpio_irq_api.o(i.gpio_irq_init)
- gpio_irq1 from gpio_irq_api.o(i.gpio_irq1) referenced from gpio_irq_api.o(i.gpio_irq_init)
- gpio_irq2 from gpio_irq_api.o(i.gpio_irq2) referenced from gpio_irq_api.o(i.gpio_irq_init)
- gpio_irq3 from gpio_irq_api.o(i.gpio_irq3) referenced from gpio_irq_api.o(i.gpio_irq_init)
- gpio_irq4 from gpio_irq_api.o(i.gpio_irq4) referenced from gpio_irq_api.o(i.gpio_irq_init)
- gpio_irq5 from gpio_irq_api.o(i.gpio_irq5) referenced from gpio_irq_api.o(i.gpio_irq_init)
- gpio_irq6 from gpio_irq_api.o(i.gpio_irq6) referenced from gpio_irq_api.o(i.gpio_irq_init)
- isspace from isspace.o(.text) referenced from scanf_char.o(.text)
- rtc_init from rtc_api.o(i.rtc_init) referenced from rtc_time.o(.data)
- rtc_isenabled from rtc_api.o(i.rtc_isenabled) referenced from rtc_time.o(.data)
- rtc_read from rtc_api.o(i.rtc_read) referenced from rtc_time.o(.data)
- rtc_write from rtc_api.o(i.rtc_write) referenced from rtc_time.o(.data)
- timer_irq_handler from hal_tick.o(i.timer_irq_handler) referenced from hal_tick.o(i.HAL_InitTick)
- uart1_irq from serial_api.o(i.uart1_irq) referenced from serial_api.o(i.serial_irq_set)
- uart2_irq from serial_api.o(i.uart2_irq) referenced from serial_api.o(i.serial_irq_set)
- uart6_irq from serial_api.o(i.uart6_irq) referenced from serial_api.o(i.serial_irq_set)
- us_ticker_clear_interrupt from us_ticker.o(i.us_ticker_clear_interrupt) referenced from us_ticker_api.o(.constdata)
- us_ticker_disable_interrupt from us_ticker.o(i.us_ticker_disable_interrupt) referenced from us_ticker_api.o(.constdata)
- us_ticker_init from us_ticker.o(i.us_ticker_init) referenced from us_ticker_api.o(.constdata)
- us_ticker_read from us_ticker.o(i.us_ticker_read) referenced from us_ticker_api.o(.constdata)
- us_ticker_set_interrupt from us_ticker.o(i.us_ticker_set_interrupt) referenced from us_ticker_api.o(.constdata)

### Global Symbols

__main (Thumb, 8 bytes, Stack size 0 bytes, __main.o(!!!main))

[Calls]

- >> __rt_entry
- >> __scatterload

__scatterload (Thumb, 0 bytes, Stack size unknown bytes, __scatter.o(!!!scatter))

[Called By]

- >> __main

__scatterload_rt2 (Thumb, 44 bytes, Stack size unknown bytes, __scatter.o(!!!scatter), UNUSED)

[Calls]

- >> __rt_entry

__scatterload_rt2_thumb_only (Thumb, 0 bytes, Stack size unknown bytes, __scatter.o(!!!scatter), UNUSED)

__scatterload_null (Thumb, 0 bytes, Stack size unknown bytes, __scatter.o(!!!scatter), UNUSED)

__scatterload_copy (Thumb, 26 bytes, Stack size unknown bytes, __scatter_copy.o(!!handler_copy), UNUSED)

[Calls]

- >> __scatterload_copy

[Called By]

- >> __scatterload_copy

__scatterload_zeroinit (Thumb, 28 bytes, Stack size unknown bytes, __scatter_zi.o(!!handler_zi), UNUSED)

_printf_n (Thumb, 0 bytes, Stack size unknown bytes, _printf_n.o(.ARM.Collect$$_printf_percent$$00000001))

[Calls]

- >> _printf_charcount

_printf_percent (Thumb, 0 bytes, Stack size unknown bytes, _printf_percent.o(.ARM.Collect$$_printf_percent$$00000000))

[Called By]

- >> __printf

_printf_p (Thumb, 0 bytes, Stack size unknown bytes, _printf_p.o(.ARM.Collect$$_printf_percent$$00000002))

[Stack]

- Max Depth = 64 + Unknown Stack Size
- Call Chain = _printf_p ⇒ _printf_hex_ptr ⇒ _printf_longlong_hex ⇒ _printf_int_common ⇒ _printf_post_padding

[Calls]

- >> _printf_hex_ptr

_printf_f (Thumb, 0 bytes, Stack size unknown bytes, _printf_f.o(.ARM.Collect$$_printf_percent$$00000003))

[Stack]

- Max Depth = 320 + Unknown Stack Size
- Call Chain = _printf_f ⇒ _printf_fp_dec ⇒ _printf_fp_dec_real ⇒ _fp_digits ⇒ _btod_etento ⇒ _btod_emul ⇒ _e2e

[Calls]

- >> _printf_fp_dec

_printf_e (Thumb, 0 bytes, Stack size unknown bytes, _printf_e.o(.ARM.Collect$$_printf_percent$$00000004))

[Stack]

- Max Depth = 320 + Unknown Stack Size
- Call Chain = _printf_e ⇒ _printf_fp_dec ⇒ _printf_fp_dec_real ⇒ _fp_digits ⇒ _btod_etento ⇒ _btod_emul ⇒ _e2e

[Calls]

- >> _printf_fp_dec

_printf_g (Thumb, 0 bytes, Stack size unknown bytes, _printf_g.o(.ARM.Collect$$_printf_percent$$00000005))

[Stack]

- Max Depth = 320 + Unknown Stack Size
- Call Chain = _printf_g ⇒ _printf_fp_dec ⇒ _printf_fp_dec_real ⇒ _fp_digits ⇒ _btod_etento ⇒ _btod_emul ⇒ _e2e

[Calls]

- >> _printf_fp_dec

_printf_a (Thumb, 0 bytes, Stack size unknown bytes, _printf_a.o(.ARM.Collect$$_printf_percent$$00000006))

[Stack]

- Max Depth = 112 + Unknown Stack Size
- Call Chain = _printf_a ⇒ _printf_fp_hex ⇒ _printf_fp_hex_real ⇒ _printf_fp_infnan ⇒ _printf_post_padding

[Calls]

- >> _printf_fp_hex

_printf_ll (Thumb, 0 bytes, Stack size unknown bytes, _printf_ll.o(.ARM.Collect$$_printf_percent$$00000007))

_printf_i (Thumb, 0 bytes, Stack size unknown bytes, _printf_i.o(.ARM.Collect$$_printf_percent$$00000008))

[Stack]

- Max Depth = 72 + Unknown Stack Size
- Call Chain = _printf_i ⇒ _printf_int_dec ⇒ _printf_int_common ⇒ _printf_post_padding

[Calls]

- >> _printf_int_dec

_printf_d (Thumb, 0 bytes, Stack size unknown bytes, _printf_d.o(.ARM.Collect$$_printf_percent$$00000009))

[Stack]

- Max Depth = 72 + Unknown Stack Size
- Call Chain = _printf_d ⇒ _printf_int_dec ⇒ _printf_int_common ⇒ _printf_post_padding

[Calls]

- >> _printf_int_dec

_printf_u (Thumb, 0 bytes, Stack size unknown bytes, _printf_u.o(.ARM.Collect$$_printf_percent$$0000000A))

[Stack]

- Max Depth = 72 + Unknown Stack Size
- Call Chain = _printf_u ⇒ _printf_int_dec ⇒ _printf_int_common ⇒ _printf_post_padding

[Calls]

- >> _printf_int_dec

_printf_o (Thumb, 0 bytes, Stack size unknown bytes, _printf_o.o(.ARM.Collect$$_printf_percent$$0000000B))

[Stack]

- Max Depth = 64 + Unknown Stack Size
- Call Chain = _printf_o ⇒ _printf_int_oct ⇒ _printf_longlong_oct ⇒ _printf_int_common ⇒ _printf_post_padding

[Calls]

- >> _printf_int_oct

_printf_x (Thumb, 0 bytes, Stack size unknown bytes, _printf_x.o(.ARM.Collect$$_printf_percent$$0000000C))

[Stack]

- Max Depth = 80 + Unknown Stack Size
- Call Chain = _printf_x ⇒ _printf_int_hex ⇒ _printf_longlong_hex ⇒ _printf_int_common ⇒ _printf_post_padding

[Calls]

- >> _printf_int_hex

_printf_lli (Thumb, 0 bytes, Stack size unknown bytes, _printf_lli.o(.ARM.Collect$$_printf_percent$$0000000D))

[Stack]

- Max Depth = 72 + Unknown Stack Size
- Call Chain = _printf_lli ⇒ _printf_longlong_dec ⇒ _printf_int_common ⇒ _printf_post_padding

[Calls]

- >> _printf_longlong_dec

_printf_lld (Thumb, 0 bytes, Stack size unknown bytes, _printf_lld.o(.ARM.Collect$$_printf_percent$$0000000E))

[Stack]

- Max Depth = 72 + Unknown Stack Size
- Call Chain = _printf_lld ⇒ _printf_longlong_dec ⇒ _printf_int_common ⇒ _printf_post_padding

[Calls]

- >> _printf_longlong_dec

_printf_llu (Thumb, 0 bytes, Stack size unknown bytes, _printf_llu.o(.ARM.Collect$$_printf_percent$$0000000F))

[Stack]

- Max Depth = 72 + Unknown Stack Size
- Call Chain = _printf_llu ⇒ _printf_longlong_dec ⇒ _printf_int_common ⇒ _printf_post_padding

[Calls]

- >> _printf_longlong_dec

_printf_llo (Thumb, 0 bytes, Stack size unknown bytes, _printf_llo.o(.ARM.Collect$$_printf_percent$$00000010))

[Stack]

- Max Depth = 56 + Unknown Stack Size
- Call Chain = _printf_llo ⇒ _printf_ll_oct ⇒ _printf_longlong_oct ⇒ _printf_int_common ⇒ _printf_post_padding

[Calls]

- >> _printf_ll_oct

_printf_llx (Thumb, 0 bytes, Stack size unknown bytes, _printf_llx.o(.ARM.Collect$$_printf_percent$$00000011))

[Stack]

- Max Depth = 64 + Unknown Stack Size
- Call Chain = _printf_llx ⇒ _printf_ll_hex ⇒ _printf_longlong_hex ⇒ _printf_int_common ⇒ _printf_post_padding

[Calls]

- >> _printf_ll_hex

_printf_l (Thumb, 0 bytes, Stack size unknown bytes, _printf_l.o(.ARM.Collect$$_printf_percent$$00000012))

_printf_c (Thumb, 0 bytes, Stack size unknown bytes, _printf_c.o(.ARM.Collect$$_printf_percent$$00000013))

[Stack]

- Max Depth = 40 + Unknown Stack Size
- Call Chain = _printf_c ⇒ _printf_char ⇒ _printf_cs_common ⇒ _printf_str ⇒ _printf_post_padding

[Calls]

- >> _printf_char

_printf_s (Thumb, 0 bytes, Stack size unknown bytes, _printf_s.o(.ARM.Collect$$_printf_percent$$00000014))

[Stack]

- Max Depth = 40 + Unknown Stack Size
- Call Chain = _printf_s ⇒ _printf_string ⇒ _printf_cs_common ⇒ _printf_str ⇒ _printf_post_padding

[Calls]

- >> _printf_string

_printf_lc (Thumb, 0 bytes, Stack size unknown bytes, _printf_lc.o(.ARM.Collect$$_printf_percent$$00000015))

[Stack]

- Max Depth = 88 + Unknown Stack Size
- Call Chain = _printf_lc ⇒ _printf_wchar ⇒ _printf_lcs_common ⇒ _printf_wctomb ⇒ _wcrtomb ⇒ __rt_ctype_table

[Calls]

- >> _printf_wchar

_printf_ls (Thumb, 0 bytes, Stack size unknown bytes, _printf_ls.o(.ARM.Collect$$_printf_percent$$00000016))

[Stack]

- Max Depth = 88 + Unknown Stack Size
- Call Chain = _printf_ls ⇒ _printf_wstring ⇒ _printf_lcs_common ⇒ _printf_wctomb ⇒ _wcrtomb ⇒ __rt_ctype_table

[Calls]

- >> _printf_wstring

_printf_percent_end (Thumb, 0 bytes, Stack size unknown bytes, _printf_percent_end.o(.ARM.Collect$$_printf_percent$$00000017))

__rt_lib_init (Thumb, 0 bytes, Stack size unknown bytes, libinit.o(.ARM.Collect$$libinit$$00000000))

[Called By]

- >> __rt_entry_li

__rt_lib_init_fp_1 (Thumb, 0 bytes, Stack size unknown bytes, libinit2.o(.ARM.Collect$$libinit$$00000001))

[Calls]

- >> _fp_init

__rt_lib_init_heap_2 (Thumb, 0 bytes, Stack size unknown bytes, libinit2.o(.ARM.Collect$$libinit$$00000005))

[Stack]

- Max Depth = 64 + Unknown Stack Size
- Call Chain = __rt_lib_init_heap_2 ⇒ _init_alloc ⇒ __rt_SIGRTMEM ⇒ __rt_SIGRTMEM_inner ⇒ __default_signal_display ⇒ _ttywrch

[Calls]

- >> _init_alloc

__rt_lib_init_preinit_1 (Thumb, 0 bytes, Stack size unknown bytes, libinit2.o(.ARM.Collect$$libinit$$00000004))

__rt_lib_init_heap_1 (Thumb, 0 bytes, Stack size unknown bytes, libinit2.o(.ARM.Collect$$libinit$$0000000A))

__rt_lib_init_lc_common (Thumb, 0 bytes, Stack size unknown bytes, libinit2.o(.ARM.Collect$$libinit$$0000000F))

[Calls]

- >> __rt_locale

__rt_lib_init_rand_1 (Thumb, 0 bytes, Stack size unknown bytes, libinit2.o(.ARM.Collect$$libinit$$0000000E))

__rt_lib_init_user_alloc_1 (Thumb, 0 bytes, Stack size unknown bytes, libinit2.o(.ARM.Collect$$libinit$$0000000C))

__rt_lib_init_lc_collate_1 (Thumb, 0 bytes, Stack size unknown bytes, libinit2.o(.ARM.Collect$$libinit$$00000011))

__rt_lib_init_lc_ctype_2 (Thumb, 0 bytes, Stack size unknown bytes, libinit2.o(.ARM.Collect$$libinit$$00000012))

[Stack]

- Max Depth = 8 + Unknown Stack Size
- Call Chain = __rt_lib_init_lc_ctype_2 ⇒ _get_lc_ctype

[Calls]

- >> _get_lc_ctype

__rt_lib_init_lc_ctype_1 (Thumb, 0 bytes, Stack size unknown bytes, libinit2.o(.ARM.Collect$$libinit$$00000013))

__rt_lib_init_lc_monetary_1 (Thumb, 0 bytes, Stack size unknown bytes, libinit2.o(.ARM.Collect$$libinit$$00000015))

__rt_lib_init_lc_numeric_2 (Thumb, 0 bytes, Stack size unknown bytes, libinit2.o(.ARM.Collect$$libinit$$00000016))

[Stack]

- Max Depth = 8 + Unknown Stack Size
- Call Chain = __rt_lib_init_lc_numeric_2 ⇒ _get_lc_numeric

[Calls]

- >> _get_lc_numeric

__rt_lib_init_atexit_1 (Thumb, 0 bytes, Stack size unknown bytes, libinit2.o(.ARM.Collect$$libinit$$0000001B))

__rt_lib_init_clock_1 (Thumb, 0 bytes, Stack size unknown bytes, libinit2.o(.ARM.Collect$$libinit$$00000021))

__rt_lib_init_fp_trap_1 (Thumb, 0 bytes, Stack size unknown bytes, libinit2.o(.ARM.Collect$$libinit$$0000001F))

__rt_lib_init_getenv_1 (Thumb, 0 bytes, Stack size unknown bytes, libinit2.o(.ARM.Collect$$libinit$$00000023))

__rt_lib_init_lc_numeric_1 (Thumb, 0 bytes, Stack size unknown bytes, libinit2.o(.ARM.Collect$$libinit$$00000017))

__rt_lib_init_lc_time_1 (Thumb, 0 bytes, Stack size unknown bytes, libinit2.o(.ARM.Collect$$libinit$$00000019))

__rt_lib_init_signal_1 (Thumb, 0 bytes, Stack size unknown bytes, libinit2.o(.ARM.Collect$$libinit$$0000001D))

__rt_lib_init_stdio_2 (Thumb, 0 bytes, Stack size unknown bytes, libinit2.o(.ARM.Collect$$libinit$$00000024))

[Stack]

- Max Depth = 560 + Unknown Stack Size
- Call Chain = __rt_lib_init_stdio_2 ⇒ _initio ⇒ freopen ⇒ _sys_open ⇒ __0sscanf ⇒ __vfscanf_char ⇒ __vfscanf ⇒ _scanf_real ⇒ _scanf_really_real ⇒ _fp_value ⇒ _btod_etento ⇒ _btod_emul ⇒ _e2e

[Calls]

- >> _initio

__rt_lib_init_alloca_1 (Thumb, 0 bytes, Stack size unknown bytes, libinit2.o(.ARM.Collect$$libinit$$0000002E))

__rt_lib_init_argv_1 (Thumb, 0 bytes, Stack size unknown bytes, libinit2.o(.ARM.Collect$$libinit$$0000002C))

__rt_lib_init_cpp_2 (Thumb, 0 bytes, Stack size unknown bytes, libinit2.o(.ARM.Collect$$libinit$$00000031))

[Stack]

- Max Depth = 16 + Unknown Stack Size
- Call Chain = __rt_lib_init_cpp_2 ⇒ __cpp_initialize__aeabi_

[Calls]

- >> __cpp_initialize__aeabi_

__rt_lib_init_exceptions_1 (Thumb, 0 bytes, Stack size unknown bytes, libinit2.o(.ARM.Collect$$libinit$$00000030))

__rt_lib_init_stdio_1 (Thumb, 0 bytes, Stack size unknown bytes, libinit2.o(.ARM.Collect$$libinit$$00000025))

__rt_lib_init_cpp_1 (Thumb, 0 bytes, Stack size unknown bytes, libinit2.o(.ARM.Collect$$libinit$$00000032))

__rt_lib_init_return (Thumb, 0 bytes, Stack size unknown bytes, libinit2.o(.ARM.Collect$$libinit$$00000033))

__rt_entry (Thumb, 0 bytes, Stack size unknown bytes, __rtentry.o(.ARM.Collect$$rtentry$$00000000))

[Called By]

- >> __main
- >> __scatterload_rt2

__rt_entry_presh_1 (Thumb, 0 bytes, Stack size unknown bytes, __rtentry2.o(.ARM.Collect$$rtentry$$00000002))

__rt_entry_sh (Thumb, 0 bytes, Stack size unknown bytes, __rtentry4.o(.ARM.Collect$$rtentry$$00000004))

[Calls]

- >> __user_setup_stackheap

__rt_lib_shutdown_cpp_2 (Thumb, 0 bytes, Stack size unknown bytes, libshutdown2.o(.ARM.Collect$$libshutdown$$00000002))

__rt_lib_shutdown_stdio_2 (Thumb, 0 bytes, Stack size unknown bytes, libshutdown2.o(.ARM.Collect$$libshutdown$$00000004))

__rt_entry_li (Thumb, 0 bytes, Stack size unknown bytes, __rtentry2.o(.ARM.Collect$$rtentry$$0000000A))

[Calls]

- >> __rt_lib_init

__rt_entry_postsh_1 (Thumb, 0 bytes, Stack size unknown bytes, __rtentry2.o(.ARM.Collect$$rtentry$$00000009))

__rt_entry_main (Thumb, 0 bytes, Stack size unknown bytes, __rtentry2.o(.ARM.Collect$$rtentry$$0000000D))

[Stack]

- Max Depth = 592 + Unknown Stack Size
- Call Chain = __rt_entry_main ⇒ main ⇒ $Super$$main ⇒ mbed::Stream::scanf(const char*, ...) ⇒ vfscanf ⇒ __vfscanf_char_file ⇒ __vfscanf_char ⇒ __vfscanf ⇒ _scanf_real ⇒ _scanf_really_real ⇒ _fp_value ⇒ _btod_etento ⇒ _btod_emul ⇒ _e2e

[Calls]

- >> exit
- >> main

__rt_entry_postli_1 (Thumb, 0 bytes, Stack size unknown bytes, __rtentry2.o(.ARM.Collect$$rtentry$$0000000C))

Reset_Handler (Thumb, 8 bytes, Stack size 0 bytes, startup_stm32f401xe.o(.text))
[Address Reference Count : 1]

- startup_stm32f401xe.o(RESET)

_maybe_terminate_alloc (Thumb, 0 bytes, Stack size 0 bytes, maybetermalloc1.o(.emb_text), UNUSED)

NMI_Handler (Thumb, 2 bytes, Stack size 0 bytes, startup_stm32f401xe.o(.text))

[Calls]

- >> NMI_Handler

[Called By]

- >> NMI_Handler

[Address Reference Count : 1]

- startup_stm32f401xe.o(RESET)

HardFault_Handler (Thumb, 2 bytes, Stack size 0 bytes, startup_stm32f401xe.o(.text))

[Calls]

- >> HardFault_Handler

[Called By]

- >> HardFault_Handler

[Address Reference Count : 1]

- startup_stm32f401xe.o(RESET)

MemManage_Handler (Thumb, 2 bytes, Stack size 0 bytes, startup_stm32f401xe.o(.text))

[Calls]

- >> MemManage_Handler

[Called By]

- >> MemManage_Handler

[Address Reference Count : 1]

- startup_stm32f401xe.o(RESET)

BusFault_Handler (Thumb, 2 bytes, Stack size 0 bytes, startup_stm32f401xe.o(.text))

[Calls]

- >> BusFault_Handler

[Called By]

- >> BusFault_Handler

[Address Reference Count : 1]

- startup_stm32f401xe.o(RESET)

UsageFault_Handler (Thumb, 2 bytes, Stack size 0 bytes, startup_stm32f401xe.o(.text))

[Calls]

- >> UsageFault_Handler

[Called By]

- >> UsageFault_Handler

[Address Reference Count : 1]

- startup_stm32f401xe.o(RESET)

SVC_Handler (Thumb, 2 bytes, Stack size 0 bytes, startup_stm32f401xe.o(.text))

[Calls]

- >> SVC_Handler

[Called By]

- >> SVC_Handler

[Address Reference Count : 1]

- startup_stm32f401xe.o(RESET)

DebugMon_Handler (Thumb, 2 bytes, Stack size 0 bytes, startup_stm32f401xe.o(.text))

[Calls]

- >> DebugMon_Handler

[Called By]

- >> DebugMon_Handler

[Address Reference Count : 1]

- startup_stm32f401xe.o(RESET)

PendSV_Handler (Thumb, 2 bytes, Stack size 0 bytes, startup_stm32f401xe.o(.text))

[Calls]

- >> PendSV_Handler

[Called By]

- >> PendSV_Handler

[Address Reference Count : 1]

- startup_stm32f401xe.o(RESET)

SysTick_Handler (Thumb, 2 bytes, Stack size 0 bytes, startup_stm32f401xe.o(.text))

[Calls]

- >> SysTick_Handler

[Called By]

- >> SysTick_Handler

[Address Reference Count : 1]

- startup_stm32f401xe.o(RESET)

ADC_IRQHandler (Thumb, 0 bytes, Stack size 0 bytes, startup_stm32f401xe.o(.text))

[Calls]

- >> ADC_IRQHandler

[Called By]

- >> ADC_IRQHandler

[Address Reference Count : 1]

- startup_stm32f401xe.o(RESET)

DMA1_Stream0_IRQHandler (Thumb, 0 bytes, Stack size 0 bytes, startup_stm32f401xe.o(.text))
[Address Reference Count : 1]

- startup_stm32f401xe.o(RESET)

DMA1_Stream1_IRQHandler (Thumb, 0 bytes, Stack size 0 bytes, startup_stm32f401xe.o(.text))
[Address Reference Count : 1]

- startup_stm32f401xe.o(RESET)

DMA1_Stream2_IRQHandler (Thumb, 0 bytes, Stack size 0 bytes, startup_stm32f401xe.o(.text))
[Address Reference Count : 1]

- startup_stm32f401xe.o(RESET)

DMA1_Stream3_IRQHandler (Thumb, 0 bytes, Stack size 0 bytes, startup_stm32f401xe.o(.text))
[Address Reference Count : 1]

- startup_stm32f401xe.o(RESET)

DMA1_Stream4_IRQHandler (Thumb, 0 bytes, Stack size 0 bytes, startup_stm32f401xe.o(.text))
[Address Reference Count : 1]

- startup_stm32f401xe.o(RESET)

DMA1_Stream5_IRQHandler (Thumb, 0 bytes, Stack size 0 bytes, startup_stm32f401xe.o(.text))
[Address Reference Count : 1]

- startup_stm32f401xe.o(RESET)

DMA1_Stream6_IRQHandler (Thumb, 0 bytes, Stack size 0 bytes, startup_stm32f401xe.o(.text))
[Address Reference Count : 1]

- startup_stm32f401xe.o(RESET)

DMA1_Stream7_IRQHandler (Thumb, 0 bytes, Stack size 0 bytes, startup_stm32f401xe.o(.text))
[Address Reference Count : 1]

- startup_stm32f401xe.o(RESET)

DMA2_Stream0_IRQHandler (Thumb, 0 bytes, Stack size 0 bytes, startup_stm32f401xe.o(.text))
[Address Reference Count : 1]

- startup_stm32f401xe.o(RESET)

DMA2_Stream1_IRQHandler (Thumb, 0 bytes, Stack size 0 bytes, startup_stm32f401xe.o(.text))
[Address Reference Count : 1]

- startup_stm32f401xe.o(RESET)

DMA2_Stream2_IRQHandler (Thumb, 0 bytes, Stack size 0 bytes, startup_stm32f401xe.o(.text))
[Address Reference Count : 1]

- startup_stm32f401xe.o(RESET)

DMA2_Stream3_IRQHandler (Thumb, 0 bytes, Stack size 0 bytes, startup_stm32f401xe.o(.text))
[Address Reference Count : 1]

- startup_stm32f401xe.o(RESET)

DMA2_Stream4_IRQHandler (Thumb, 0 bytes, Stack size 0 bytes, startup_stm32f401xe.o(.text))
[Address Reference Count : 1]

- startup_stm32f401xe.o(RESET)

DMA2_Stream5_IRQHandler (Thumb, 0 bytes, Stack size 0 bytes, startup_stm32f401xe.o(.text))
[Address Reference Count : 1]

- startup_stm32f401xe.o(RESET)

DMA2_Stream6_IRQHandler (Thumb, 0 bytes, Stack size 0 bytes, startup_stm32f401xe.o(.text))
[Address Reference Count : 1]

- startup_stm32f401xe.o(RESET)

DMA2_Stream7_IRQHandler (Thumb, 0 bytes, Stack size 0 bytes, startup_stm32f401xe.o(.text))
[Address Reference Count : 1]

- startup_stm32f401xe.o(RESET)

EXTI0_IRQHandler (Thumb, 0 bytes, Stack size 0 bytes, startup_stm32f401xe.o(.text))
[Address Reference Count : 1]

- startup_stm32f401xe.o(RESET)

EXTI15_10_IRQHandler (Thumb, 0 bytes, Stack size 0 bytes, startup_stm32f401xe.o(.text))
[Address Reference Count : 1]

- startup_stm32f401xe.o(RESET)

EXTI1_IRQHandler (Thumb, 0 bytes, Stack size 0 bytes, startup_stm32f401xe.o(.text))
[Address Reference Count : 1]

- startup_stm32f401xe.o(RESET)

EXTI2_IRQHandler (Thumb, 0 bytes, Stack size 0 bytes, startup_stm32f401xe.o(.text))
[Address Reference Count : 1]

- startup_stm32f401xe.o(RESET)

EXTI3_IRQHandler (Thumb, 0 bytes, Stack size 0 bytes, startup_stm32f401xe.o(.text))
[Address Reference Count : 1]

- startup_stm32f401xe.o(RESET)

EXTI4_IRQHandler (Thumb, 0 bytes, Stack size 0 bytes, startup_stm32f401xe.o(.text))
[Address Reference Count : 1]

- startup_stm32f401xe.o(RESET)

EXTI9_5_IRQHandler (Thumb, 0 bytes, Stack size 0 bytes, startup_stm32f401xe.o(.text))
[Address Reference Count : 1]

- startup_stm32f401xe.o(RESET)

FLASH_IRQHandler (Thumb, 0 bytes, Stack size 0 bytes, startup_stm32f401xe.o(.text))
[Address Reference Count : 1]

- startup_stm32f401xe.o(RESET)

FPU_IRQHandler (Thumb, 0 bytes, Stack size 0 bytes, startup_stm32f401xe.o(.text))
[Address Reference Count : 1]

- startup_stm32f401xe.o(RESET)

I2C1_ER_IRQHandler (Thumb, 0 bytes, Stack size 0 bytes, startup_stm32f401xe.o(.text))
[Address Reference Count : 1]

- startup_stm32f401xe.o(RESET)

I2C1_EV_IRQHandler (Thumb, 0 bytes, Stack size 0 bytes, startup_stm32f401xe.o(.text))
[Address Reference Count : 1]

- startup_stm32f401xe.o(RESET)

I2C2_ER_IRQHandler (Thumb, 0 bytes, Stack size 0 bytes, startup_stm32f401xe.o(.text))
[Address Reference Count : 1]

- startup_stm32f401xe.o(RESET)

I2C2_EV_IRQHandler (Thumb, 0 bytes, Stack size 0 bytes, startup_stm32f401xe.o(.text))
[Address Reference Count : 1]

- startup_stm32f401xe.o(RESET)

I2C3_ER_IRQHandler (Thumb, 0 bytes, Stack size 0 bytes, startup_stm32f401xe.o(.text))
[Address Reference Count : 1]

- startup_stm32f401xe.o(RESET)

I2C3_EV_IRQHandler (Thumb, 0 bytes, Stack size 0 bytes, startup_stm32f401xe.o(.text))
[Address Reference Count : 1]

- startup_stm32f401xe.o(RESET)

OTG_FS_IRQHandler (Thumb, 0 bytes, Stack size 0 bytes, startup_stm32f401xe.o(.text))
[Address Reference Count : 1]

- startup_stm32f401xe.o(RESET)

OTG_FS_WKUP_IRQHandler (Thumb, 0 bytes, Stack size 0 bytes, startup_stm32f401xe.o(.text))
[Address Reference Count : 1]

- startup_stm32f401xe.o(RESET)

PVD_IRQHandler (Thumb, 0 bytes, Stack size 0 bytes, startup_stm32f401xe.o(.text))
[Address Reference Count : 1]

- startup_stm32f401xe.o(RESET)

RCC_IRQHandler (Thumb, 0 bytes, Stack size 0 bytes, startup_stm32f401xe.o(.text))
[Address Reference Count : 1]

- startup_stm32f401xe.o(RESET)

RTC_Alarm_IRQHandler (Thumb, 0 bytes, Stack size 0 bytes, startup_stm32f401xe.o(.text))
[Address Reference Count : 1]

- startup_stm32f401xe.o(RESET)

RTC_WKUP_IRQHandler (Thumb, 0 bytes, Stack size 0 bytes, startup_stm32f401xe.o(.text))
[Address Reference Count : 1]

- startup_stm32f401xe.o(RESET)

SDIO_IRQHandler (Thumb, 0 bytes, Stack size 0 bytes, startup_stm32f401xe.o(.text))
[Address Reference Count : 1]

- startup_stm32f401xe.o(RESET)

SPI1_IRQHandler (Thumb, 0 bytes, Stack size 0 bytes, startup_stm32f401xe.o(.text))
[Address Reference Count : 1]

- startup_stm32f401xe.o(RESET)

SPI2_IRQHandler (Thumb, 0 bytes, Stack size 0 bytes, startup_stm32f401xe.o(.text))
[Address Reference Count : 1]

- startup_stm32f401xe.o(RESET)

SPI3_IRQHandler (Thumb, 0 bytes, Stack size 0 bytes, startup_stm32f401xe.o(.text))
[Address Reference Count : 1]

- startup_stm32f401xe.o(RESET)

SPI4_IRQHandler (Thumb, 0 bytes, Stack size 0 bytes, startup_stm32f401xe.o(.text))
[Address Reference Count : 1]

- startup_stm32f401xe.o(RESET)

TAMP_STAMP_IRQHandler (Thumb, 0 bytes, Stack size 0 bytes, startup_stm32f401xe.o(.text))
[Address Reference Count : 1]

- startup_stm32f401xe.o(RESET)

TIM1_BRK_TIM9_IRQHandler (Thumb, 0 bytes, Stack size 0 bytes, startup_stm32f401xe.o(.text))
[Address Reference Count : 1]

- startup_stm32f401xe.o(RESET)

TIM1_CC_IRQHandler (Thumb, 0 bytes, Stack size 0 bytes, startup_stm32f401xe.o(.text))
[Address Reference Count : 1]

- startup_stm32f401xe.o(RESET)

TIM1_TRG_COM_TIM11_IRQHandler (Thumb, 0 bytes, Stack size 0 bytes, startup_stm32f401xe.o(.text))
[Address Reference Count : 1]

- startup_stm32f401xe.o(RESET)

TIM1_UP_TIM10_IRQHandler (Thumb, 0 bytes, Stack size 0 bytes, startup_stm32f401xe.o(.text))
[Address Reference Count : 1]

- startup_stm32f401xe.o(RESET)

TIM2_IRQHandler (Thumb, 0 bytes, Stack size 0 bytes, startup_stm32f401xe.o(.text))
[Address Reference Count : 1]

- startup_stm32f401xe.o(RESET)

TIM3_IRQHandler (Thumb, 0 bytes, Stack size 0 bytes, startup_stm32f401xe.o(.text))
[Address Reference Count : 1]

- startup_stm32f401xe.o(RESET)

TIM4_IRQHandler (Thumb, 0 bytes, Stack size 0 bytes, startup_stm32f401xe.o(.text))
[Address Reference Count : 1]

- startup_stm32f401xe.o(RESET)

TIM5_IRQHandler (Thumb, 0 bytes, Stack size 0 bytes, startup_stm32f401xe.o(.text))
[Address Reference Count : 1]

- startup_stm32f401xe.o(RESET)

USART1_IRQHandler (Thumb, 0 bytes, Stack size 0 bytes, startup_stm32f401xe.o(.text))
[Address Reference Count : 1]

- startup_stm32f401xe.o(RESET)

USART2_IRQHandler (Thumb, 0 bytes, Stack size 0 bytes, startup_stm32f401xe.o(.text))
[Address Reference Count : 1]

- startup_stm32f401xe.o(RESET)

USART6_IRQHandler (Thumb, 0 bytes, Stack size 0 bytes, startup_stm32f401xe.o(.text))
[Address Reference Count : 1]

- startup_stm32f401xe.o(RESET)

WWDG_IRQHandler (Thumb, 0 bytes, Stack size 0 bytes, startup_stm32f401xe.o(.text))
[Address Reference Count : 1]

- startup_stm32f401xe.o(RESET)

malloc (Thumb, 94 bytes, Stack size 16 bytes, h1_alloc.o(.text))

[Stack]

- Max Depth = 48
- Call Chain = malloc ⇒ __Heap_Full ⇒ __Heap_ProvideMemory ⇒ free

[Calls]

- >> __Heap_Full
- >> __rt_heap_descriptor

[Called By]

- >> AjK::MODSERIAL::init(int, int, PinName)
- >> operator new(unsigned)
- >> __aeabi_atexit
- >> fopen
- >> __cxa_get_globals
- >> __flsbuf
- >> __filbuf
- >> __ARM_exceptions_buffer_init

free (Thumb, 78 bytes, Stack size 16 bytes, h1_free.o(.text))

[Stack]

- Max Depth = 16
- Call Chain = free

[Calls]

- >> __rt_heap_descriptor

[Called By]

- >> AjK::MODSERIAL::~MODSERIAL()
- >> operator delete (void*)
- >> _fclose_internal
- >> __Heap_ProvideMemory
- >> __cxa_finalize
- >> _terminateio

vfprintf (Thumb, 10 bytes, Stack size 0 bytes, vfprintf.o(.text))

[Stack]

- Max Depth = 120 + Unknown Stack Size
- Call Chain = vfprintf ⇒ _printf_char_file ⇒ _printf_char_common ⇒ __printf

[Calls]

- >> _printf_char_file

[Called By]

- >> error

__c89vfprintf (Thumb, 10 bytes, Stack size 0 bytes, c89vfprintf.o(.text))

[Stack]

- Max Depth = 120 + Unknown Stack Size
- Call Chain = __c89vfprintf ⇒ _printf_char_file ⇒ _printf_char_common ⇒ __printf

[Calls]

- >> _printf_char_file

[Called By]

- >> mbed::Stream::printf(const char*, ...)

__2sprintf (Thumb, 38 bytes, Stack size 32 bytes, __2sprintf.o(.text))

[Stack]

- Max Depth = 136 + Unknown Stack Size
- Call Chain = __2sprintf ⇒ _printf_char_common ⇒ __printf

[Calls]

- >> _sputc
- >> _printf_char_common

[Called By]

- >> mbed::Stream::Stream__sub_object(const char*)

_printf_str (Thumb, 82 bytes, Stack size 16 bytes, _printf_str.o(.text))

[Stack]

- Max Depth = 32
- Call Chain = _printf_str ⇒ _printf_post_padding

[Calls]

- >> _printf_post_padding
- >> _printf_pre_padding

[Called By]

- >> _printf_cs_common

_printf_longlong_hex (Thumb, 86 bytes, Stack size 16 bytes, _printf_hex_int_ll_ptr.o(.text))

[Stack]

- Max Depth = 64
- Call Chain = _printf_longlong_hex ⇒ _printf_int_common ⇒ _printf_post_padding

[Calls]

- >> _printf_int_common

[Called By]

- >> _printf_hex_ptr
- >> _printf_ll_hex
- >> _printf_int_hex

_printf_int_hex (Thumb, 28 bytes, Stack size 16 bytes, _printf_hex_int_ll_ptr.o(.text))

[Stack]

- Max Depth = 80
- Call Chain = _printf_int_hex ⇒ _printf_longlong_hex ⇒ _printf_int_common ⇒ _printf_post_padding

[Calls]

- >> _printf_truncate_unsigned
- >> _printf_longlong_hex

[Called By]

- >> _printf_x

_printf_ll_hex (Thumb, 12 bytes, Stack size 0 bytes, _printf_hex_int_ll_ptr.o(.text))

[Stack]

- Max Depth = 64
- Call Chain = _printf_ll_hex ⇒ _printf_longlong_hex ⇒ _printf_int_common ⇒ _printf_post_padding

[Calls]

- >> _printf_longlong_hex

[Called By]

- >> _printf_llx

_printf_hex_ptr (Thumb, 18 bytes, Stack size 0 bytes, _printf_hex_int_ll_ptr.o(.text))

[Stack]

- Max Depth = 64
- Call Chain = _printf_hex_ptr ⇒ _printf_longlong_hex ⇒ _printf_int_common ⇒ _printf_post_padding

[Calls]

- >> _printf_longlong_hex

[Called By]

- >> _printf_p

__printf (Thumb, 388 bytes, Stack size 40 bytes, __printf_flags_ss_wp.o(.text))

[Stack]

- Max Depth = 40 + Unknown Stack Size
- Call Chain = __printf

[Calls]

- >> _printf_percent
- >> _is_digit

[Called By]

- >> _printf_char_common

vfscanf (Thumb, 16 bytes, Stack size 40 bytes, vfscanf.o(.text))

[Stack]

- Max Depth = 464
- Call Chain = vfscanf ⇒ __vfscanf_char_file ⇒ __vfscanf_char ⇒ __vfscanf ⇒ _scanf_real ⇒ _scanf_really_real ⇒ _fp_value ⇒ _btod_etento ⇒ _btod_emul ⇒ _e2e

[Calls]

- >> __vfscanf_char_file

[Called By]

- >> mbed::Stream::scanf(const char*, ...)

__0sscanf (Thumb, 52 bytes, Stack size 72 bytes, __0sscanf.o(.text))

[Stack]

- Max Depth = 496
- Call Chain = __0sscanf ⇒ __vfscanf_char ⇒ __vfscanf ⇒ _scanf_real ⇒ _scanf_really_real ⇒ _fp_value ⇒ _btod_etento ⇒ _btod_emul ⇒ _e2e

[Calls]

- >> __vfscanf_char

[Called By]

- >> $Super$$main
- >> _sys_open

_scanf_int (Thumb, 332 bytes, Stack size 56 bytes, _scanf_int.o(.text))

[Stack]

- Max Depth = 56
- Call Chain = _scanf_int

[Calls]

- >> _chval

[Called By]

- >> __vfscanf

_scanf_string (Thumb, 224 bytes, Stack size 56 bytes, _scanf_str.o(.text))

[Stack]

- Max Depth = 56
- Call Chain = _scanf_string

[Called By]

- >> __vfscanf

_do_fflush (Thumb, 54 bytes, Stack size 16 bytes, fflush.o(.text))

[Stack]

- Max Depth = 200
- Call Chain = _do_fflush ⇒ _fflush ⇒ _writebuf ⇒ _sys_write ⇒ serial_init ⇒ mbed_assert_internal (Cycle)

[Calls]

- >> _fflush
- >> _fseek

[Called By]

- >> fflush
- >> _flushlinebuffered

fflush (Thumb, 42 bytes, Stack size 16 bytes, fflush.o(.text))

[Stack]

- Max Depth = 216
- Call Chain = fflush ⇒ _do_fflush ⇒ _fflush ⇒ _writebuf ⇒ _sys_write ⇒ serial_init ⇒ mbed_assert_internal (Cycle)

[Calls]

- >> _do_fflush

[Called By]

- >> mbed::Stream::printf(const char*, ...)
- >> mbed::Stream::scanf(const char*, ...)
- >> mbed::Stream::putc(int)
- >> exit

setvbuf (Thumb, 70 bytes, Stack size 16 bytes, setvbuf.o(.text))

[Stack]

- Max Depth = 16
- Call Chain = setvbuf

[Called By]

- >> setbuf
- >> _initio

freopen (Thumb, 158 bytes, Stack size 24 bytes, fopen.o(.text))

[Stack]

- Max Depth = 552
- Call Chain = freopen ⇒ _sys_open ⇒ __0sscanf ⇒ __vfscanf_char ⇒ __vfscanf ⇒ _scanf_real ⇒ _scanf_really_real ⇒ _fp_value ⇒ _btod_etento ⇒ _btod_emul ⇒ _e2e

[Calls]

- >> _sys_open
- >> _fclose_internal
- >> _fseek

[Called By]

- >> fopen
- >> _initio

fopen (Thumb, 74 bytes, Stack size 24 bytes, fopen.o(.text))

[Stack]

- Max Depth = 576
- Call Chain = fopen ⇒ freopen ⇒ _sys_open ⇒ __0sscanf ⇒ __vfscanf_char ⇒ __vfscanf ⇒ _scanf_real ⇒ _scanf_really_real ⇒ _fp_value ⇒ _btod_etento ⇒ _btod_emul ⇒ _e2e

[Calls]

- >> malloc
- >> __aeabi_memclr4
- >> freopen

[Called By]

- >> mbed::Stream::Stream__sub_object(const char*)

setbuf (Thumb, 20 bytes, Stack size 0 bytes, setbuf.o(.text))

[Stack]

- Max Depth = 16
- Call Chain = setbuf ⇒ setvbuf

[Calls]

- >> setvbuf

[Called By]

- >> mbed::mbed_set_unbuffered_stream(std::__FILE*)

_fclose_internal (Thumb, 76 bytes, Stack size 32 bytes, fclose.o(.text))

[Stack]

- Max Depth = 216
- Call Chain = _fclose_internal ⇒ _fflush ⇒ _writebuf ⇒ _sys_write ⇒ serial_init ⇒ mbed_assert_internal (Cycle)

[Calls]

- >> _sys_close
- >> free
- >> __aeabi_memclr4
- >> _fflush

[Called By]

- >> freopen
- >> _terminateio

fclose (Thumb, 0 bytes, Stack size 32 bytes, fclose.o(.text))

[Stack]

- Max Depth = 32
- Call Chain = fclose

[Called By]

- >> mbed::Stream::~Stream__sub_object()

__aeabi_atexit (Thumb, 46 bytes, Stack size 24 bytes, aeabi_atexit.o(.text))

[Stack]

- Max Depth = 72
- Call Chain = __aeabi_atexit ⇒ malloc ⇒ __Heap_Full ⇒ __Heap_ProvideMemory ⇒ free

[Calls]

- >> malloc
- >> __rt_ddtor_pointer_addr

[Called By]

- >> __sti___18_ModbusSlave232_cpp_pc
- >> __sti___8_main_cpp_led1
- >> __sti___10_millis_cpp_d9fd33a2

strlen (Thumb, 62 bytes, Stack size 8 bytes, strlen.o(.text))

[Stack]

- Max Depth = 8
- Call Chain = strlen

[Called By]

- >> mbed::FileBase::lookup(const char*, unsigned)

strncmp (Thumb, 150 bytes, Stack size 16 bytes, strncmp.o(.text))

[Stack]

- Max Depth = 16
- Call Chain = strncmp

[Called By]

- >> mbed::FileBase::lookup(const char*, unsigned)

__aeabi_memcpy4 (Thumb, 0 bytes, Stack size 8 bytes, rt_memcpy_w.o(.text))

[Stack]

- Max Depth = 8
- Call Chain = __aeabi_memcpy4

[Called By]

- >> NVIC_SetVector

__aeabi_memcpy8 (Thumb, 0 bytes, Stack size 8 bytes, rt_memcpy_w.o(.text), UNUSED)

__rt_memcpy_w (Thumb, 100 bytes, Stack size 8 bytes, rt_memcpy_w.o(.text), UNUSED)

_memcpy_lastbytes_aligned (Thumb, 0 bytes, Stack size unknown bytes, rt_memcpy_w.o(.text), UNUSED)

__aeabi_memclr4 (Thumb, 0 bytes, Stack size 4 bytes, rt_memclr_w.o(.text))

[Stack]

- Max Depth = 4
- Call Chain = __aeabi_memclr4

[Called By]

- >> DHT::readData()
- >> _fclose_internal
- >> fopen
- >> _localtime_r
- >> _initio

__aeabi_memclr8 (Thumb, 0 bytes, Stack size 4 bytes, rt_memclr_w.o(.text), UNUSED)

__rt_memclr_w (Thumb, 78 bytes, Stack size 4 bytes, rt_memclr_w.o(.text), UNUSED)

_memset_w (Thumb, 0 bytes, Stack size unknown bytes, rt_memclr_w.o(.text), UNUSED)

strcmp (Thumb, 128 bytes, Stack size 0 bytes, strcmpv7m.o(.text))

[Called By]

- >> _sys_open
- >> _get_lc_ctype
- >> _get_lc_numeric

localtime (Thumb, 6 bytes, Stack size 0 bytes, localtime.o(.text))

[Stack]

- Max Depth = 20
- Call Chain = localtime ⇒ _localtime_r ⇒ __aeabi_memclr4

[Calls]

- >> _localtime_r

[Called By]

- >> rtc_write

mktime (Thumb, 352 bytes, Stack size 56 bytes, mktime.o(.text))

[Stack]

- Max Depth = 64
- Call Chain = mktime ⇒ _tm_carry

[Calls]

- >> _tm_carry

[Called By]

- >> rtc_read

__cpp_initialize__aeabi_ (Thumb, 26 bytes, Stack size 16 bytes, init_aeabi.o(.text))

[Stack]

- Max Depth = 16
- Call Chain = __cpp_initialize__aeabi_

[Called By]

- >> __rt_lib_init_cpp_2

__rt_heap_descriptor (Thumb, 8 bytes, Stack size 0 bytes, rt_heap_descriptor.o(.text))

[Called By]

- >> free
- >> malloc
- >> _init_alloc

__rt_new_handler_addr (Thumb, 8 bytes, Stack size 0 bytes, rt_new_handler_addr.o(.text))

[Called By]

- >> operator new(unsigned)

__rt_ddtor_pointer_addr (Thumb, 8 bytes, Stack size 0 bytes, rt_ddtor_pointer_addr.o(.text))

[Called By]

- >> __aeabi_atexit
- >> __cxa_finalize

__use_no_heap (Thumb, 2 bytes, Stack size 0 bytes, hguard.o(.text), UNUSED)

__heap$guard (Thumb, 2 bytes, Stack size 0 bytes, hguard.o(.text), UNUSED)

_terminate_user_alloc (Thumb, 2 bytes, Stack size 0 bytes, init_alloc.o(.text), UNUSED)

_init_user_alloc (Thumb, 2 bytes, Stack size 0 bytes, init_alloc.o(.text), UNUSED)

__Heap_Full (Thumb, 34 bytes, Stack size 16 bytes, init_alloc.o(.text))

[Stack]

- Max Depth = 32
- Call Chain = __Heap_Full ⇒ __Heap_ProvideMemory ⇒ free

[Calls]

- >> __rt_heap_expand
- >> __Heap_ProvideMemory

[Called By]

- >> malloc

__Heap_Broken (Thumb, 6 bytes, Stack size 0 bytes, init_alloc.o(.text), UNUSED)

[Calls]

- >> __rt_SIGRTMEM

_init_alloc (Thumb, 94 bytes, Stack size 24 bytes, init_alloc.o(.text))

[Stack]

- Max Depth = 64
- Call Chain = _init_alloc ⇒ __rt_SIGRTMEM ⇒ __rt_SIGRTMEM_inner ⇒ __default_signal_display ⇒ _ttywrch

[Calls]

- >> __Heap_Initialize
- >> __rt_heap_descriptor
- >> __rt_heap_expand
- >> __rt_heap_escrow
- >> __rt_SIGRTMEM
- >> __Heap_ProvideMemory

[Called By]

- >> __rt_lib_init_heap_2

__Heap_Initialize (Thumb, 10 bytes, Stack size 0 bytes, h1_init.o(.text))

[Called By]

- >> _init_alloc

__Heap_DescSize (Thumb, 4 bytes, Stack size 0 bytes, h1_init.o(.text), UNUSED)

__read_errno (Thumb, 10 bytes, Stack size 8 bytes, _rserrno.o(.text), UNUSED)

[Calls]

- >> __aeabi_errno_addr

__set_errno (Thumb, 12 bytes, Stack size 8 bytes, _rserrno.o(.text))

[Stack]

- Max Depth = 8
- Call Chain = __set_errno

[Calls]

- >> __aeabi_errno_addr

[Called By]

- >> __hardfp_pow
- >> sqrt
- >> __hardfp_ldexp
- >> __mathlib_narrow

_printf_pre_padding (Thumb, 44 bytes, Stack size 16 bytes, _printf_pad.o(.text))

[Stack]

- Max Depth = 16
- Call Chain = _printf_pre_padding

[Called By]

- >> _printf_wctomb
- >> _printf_int_common
- >> _printf_str
- >> _printf_fp_infnan
- >> _printf_fp_hex_real
- >> _printf_fp_dec_real

_printf_post_padding (Thumb, 34 bytes, Stack size 16 bytes, _printf_pad.o(.text))

[Stack]

- Max Depth = 16
- Call Chain = _printf_post_padding

[Called By]

- >> _printf_wctomb
- >> _printf_int_common
- >> _printf_str
- >> _printf_fp_infnan
- >> _printf_fp_hex_real
- >> _printf_fp_dec_real

_printf_truncate_signed (Thumb, 18 bytes, Stack size 0 bytes, _printf_truncate.o(.text))

[Called By]

- >> _printf_int_dec

_printf_truncate_unsigned (Thumb, 18 bytes, Stack size 0 bytes, _printf_truncate.o(.text))

[Called By]

- >> _printf_int_oct
- >> _printf_int_dec
- >> _printf_int_hex

_printf_int_common (Thumb, 178 bytes, Stack size 32 bytes, _printf_intcommon.o(.text))

[Stack]

- Max Depth = 48
- Call Chain = _printf_int_common ⇒ _printf_post_padding

[Calls]

- >> _printf_post_padding
- >> _printf_pre_padding

[Called By]

- >> _printf_longlong_oct
- >> _printf_longlong_dec
- >> _printf_int_dec
- >> _printf_longlong_hex

_printf_int_dec (Thumb, 104 bytes, Stack size 24 bytes, _printf_dec.o(.text))

[Stack]

- Max Depth = 72
- Call Chain = _printf_int_dec ⇒ _printf_int_common ⇒ _printf_post_padding

[Calls]

- >> _printf_int_common
- >> _printf_truncate_unsigned
- >> _printf_truncate_signed

[Called By]

- >> _printf_d
- >> _printf_i
- >> _printf_u

_printf_charcount (Thumb, 40 bytes, Stack size 0 bytes, _printf_charcount.o(.text))

[Called By]

- >> _printf_n

_printf_char_common (Thumb, 32 bytes, Stack size 64 bytes, _printf_char_common.o(.text))

[Stack]

- Max Depth = 104 + Unknown Stack Size
- Call Chain = _printf_char_common ⇒ __printf

[Calls]

- >> __printf

[Called By]

- >> _printf_char_file
- >> __2sprintf

_sputc (Thumb, 10 bytes, Stack size 0 bytes, _sputc.o(.text))

[Called By]

- >> __2sprintf

[Address Reference Count : 1]

- __2sprintf.o(.text)

_printf_cs_common (Thumb, 20 bytes, Stack size 8 bytes, _printf_char.o(.text))

[Stack]

- Max Depth = 40
- Call Chain = _printf_cs_common ⇒ _printf_str ⇒ _printf_post_padding

[Calls]

- >> _printf_str

[Called By]

- >> _printf_string
- >> _printf_char

_printf_char (Thumb, 16 bytes, Stack size 0 bytes, _printf_char.o(.text))

[Stack]

- Max Depth = 40
- Call Chain = _printf_char ⇒ _printf_cs_common ⇒ _printf_str ⇒ _printf_post_padding

[Calls]

- >> _printf_cs_common

[Called By]

- >> _printf_c

_printf_string (Thumb, 8 bytes, Stack size 0 bytes, _printf_char.o(.text))

[Stack]

- Max Depth = 40
- Call Chain = _printf_string ⇒ _printf_cs_common ⇒ _printf_str ⇒ _printf_post_padding

[Calls]

- >> _printf_cs_common

[Called By]

- >> _printf_s

_printf_char_file (Thumb, 32 bytes, Stack size 16 bytes, _printf_char_file.o(.text))

[Stack]

- Max Depth = 120 + Unknown Stack Size
- Call Chain = _printf_char_file ⇒ _printf_char_common ⇒ __printf

[Calls]

- >> _printf_char_common
- >> ferror

[Called By]

- >> vfprintf
- >> __c89vfprintf

_printf_wctomb (Thumb, 182 bytes, Stack size 56 bytes, _printf_wctomb.o(.text))

[Stack]

- Max Depth = 80
- Call Chain = _printf_wctomb ⇒ _wcrtomb ⇒ __rt_ctype_table

[Calls]

- >> _printf_post_padding
- >> _printf_pre_padding
- >> _wcrtomb

[Called By]

- >> _printf_lcs_common

_printf_longlong_dec (Thumb, 108 bytes, Stack size 24 bytes, _printf_longlong_dec.o(.text))

[Stack]

- Max Depth = 72
- Call Chain = _printf_longlong_dec ⇒ _printf_int_common ⇒ _printf_post_padding

[Calls]

- >> _printf_int_common
- >> _ll_udiv10

[Called By]

- >> _printf_llu
- >> _printf_lld
- >> _printf_lli

_printf_longlong_oct (Thumb, 68 bytes, Stack size 8 bytes, _printf_oct_int_ll.o(.text))

[Stack]

- Max Depth = 56
- Call Chain = _printf_longlong_oct ⇒ _printf_int_common ⇒ _printf_post_padding

[Calls]

- >> _printf_int_common

[Called By]

- >> _printf_ll_oct
- >> _printf_int_oct

_printf_int_oct (Thumb, 24 bytes, Stack size 8 bytes, _printf_oct_int_ll.o(.text))

[Stack]

- Max Depth = 64
- Call Chain = _printf_int_oct ⇒ _printf_longlong_oct ⇒ _printf_int_common ⇒ _printf_post_padding

[Calls]

- >> _printf_longlong_oct
- >> _printf_truncate_unsigned

[Called By]

- >> _printf_o

_printf_ll_oct (Thumb, 12 bytes, Stack size 0 bytes, _printf_oct_int_ll.o(.text))

[Stack]

- Max Depth = 56
- Call Chain = _printf_ll_oct ⇒ _printf_longlong_oct ⇒ _printf_int_common ⇒ _printf_post_padding

[Calls]

- >> _printf_longlong_oct

[Called By]

- >> _printf_llo

_chval (Thumb, 28 bytes, Stack size 0 bytes, _chval.o(.text))

[Called By]

- >> _scanf_int
- >> _scanf_longlong
- >> _scanf_really_hex_real

_scanf_longlong (Thumb, 342 bytes, Stack size 56 bytes, _scanf_longlong.o(.text))

[Stack]

- Max Depth = 56
- Call Chain = _scanf_longlong

[Calls]

- >> _chval

[Called By]

- >> __vfscanf

__vfscanf_char (Thumb, 24 bytes, Stack size 0 bytes, scanf_char.o(.text))

[Stack]

- Max Depth = 424
- Call Chain = __vfscanf_char ⇒ __vfscanf ⇒ _scanf_real ⇒ _scanf_really_real ⇒ _fp_value ⇒ _btod_etento ⇒ _btod_emul ⇒ _e2e

[Calls]

- >> __vfscanf

[Called By]

- >> __0sscanf
- >> __vfscanf_char_file

_sgetc (Thumb, 30 bytes, Stack size 0 bytes, _sgetc.o(.text))
[Address Reference Count : 1]

- __0sscanf.o(.text)

_sbackspace (Thumb, 34 bytes, Stack size 0 bytes, _sgetc.o(.text))
[Address Reference Count : 1]

- __0sscanf.o(.text)

__vfscanf_char_file (Thumb, 16 bytes, Stack size 0 bytes, scanf_char_file.o(.text))

[Stack]

- Max Depth = 424
- Call Chain = __vfscanf_char_file ⇒ __vfscanf_char ⇒ __vfscanf ⇒ _scanf_real ⇒ _scanf_really_real ⇒ _fp_value ⇒ _btod_etento ⇒ _btod_emul ⇒ _e2e

[Calls]

- >> __vfscanf_char

[Called By]

- >> vfscanf

_scanf_mbtowc (Thumb, 276 bytes, Stack size 64 bytes, _scanf_mbtowc.o(.text))

[Stack]

- Max Depth = 88
- Call Chain = _scanf_mbtowc ⇒ _mbrtowc ⇒ __rt_ctype_table

[Calls]

- >> _mbrtowc

[Called By]

- >> __vfscanf

_scanf_wctomb (Thumb, 232 bytes, Stack size 64 bytes, _scanf_wctomb.o(.text))

[Stack]

- Max Depth = 88
- Call Chain = _scanf_wctomb ⇒ _wcrtomb ⇒ __rt_ctype_table

[Calls]

- >> _wcrtomb
- >> _scanf_wcharmap

[Called By]

- >> __vfscanf

_scanf_wstring (Thumb, 208 bytes, Stack size 56 bytes, _scanf_wstr.o(.text))

[Stack]

- Max Depth = 64
- Call Chain = _scanf_wstring ⇒ _scanf_wcharmap

[Calls]

- >> _scanf_wcharmap

[Called By]

- >> __vfscanf

ferror (Thumb, 8 bytes, Stack size 0 bytes, ferror.o(.text))

[Called By]

- >> _printf_char_file

_readbuf (Thumb, 54 bytes, Stack size 16 bytes, filbuf.o(.text), UNUSED)

[Calls]

- >> _sys_read
- >> _seterr

[Called By]

- >> __filbuf

_seteof (Thumb, 40 bytes, Stack size 0 bytes, filbuf.o(.text), UNUSED)

[Called By]

- >> __filbuf

__filbuf (Thumb, 476 bytes, Stack size 32 bytes, filbuf.o(.text), UNUSED)

[Calls]

- >> _sys_seek
- >> malloc
- >> _flushlinebuffered
- >> _deferredlazyseek
- >> _fflush
- >> _seterr
- >> _seteof
- >> _readbuf

__filbuf_byte (Thumb, 0 bytes, Stack size 32 bytes, filbuf.o(.text))

[Stack]

- Max Depth = 32
- Call Chain = __filbuf_byte

[Called By]

- >> fgetc

__filbuf_wide (Thumb, 0 bytes, Stack size 32 bytes, filbuf.o(.text), UNUSED)

__flsbuf (Thumb, 470 bytes, Stack size 32 bytes, flsbuf.o(.text), UNUSED)

[Calls]

- >> _sys_istty
- >> _sys_flen
- >> malloc
- >> _deferredlazyseek
- >> _writebuf
- >> _seterr

__flsbuf_byte (Thumb, 0 bytes, Stack size 32 bytes, flsbuf.o(.text))

[Stack]

- Max Depth = 32
- Call Chain = __flsbuf_byte

[Called By]

- >> fputc

__flsbuf_wide (Thumb, 0 bytes, Stack size 32 bytes, flsbuf.o(.text), UNUSED)

_fseek (Thumb, 242 bytes, Stack size 24 bytes, fseek.o(.text))

[Stack]

- Max Depth = 32
- Call Chain = _fseek ⇒ _ftell_internal

[Calls]

- >> _sys_istty
- >> _sys_flen
- >> _ftell_internal
- >> _seterr

[Called By]

- >> freopen
- >> _do_fflush

fseek (Thumb, 0 bytes, Stack size 24 bytes, fseek.o(.text), UNUSED)

_seterr (Thumb, 20 bytes, Stack size 0 bytes, stdio.o(.text))

[Called By]

- >> _writebuf
- >> _fseek
- >> __flsbuf
- >> __filbuf
- >> _readbuf

_writebuf (Thumb, 84 bytes, Stack size 32 bytes, stdio.o(.text))

[Stack]

- Max Depth = 168
- Call Chain = _writebuf ⇒ _sys_write ⇒ serial_init ⇒ mbed_assert_internal (Cycle)

[Calls]

- >> _sys_write
- >> _sys_seek
- >> _seterr

[Called By]

- >> _fflush
- >> __flsbuf

_fflush (Thumb, 70 bytes, Stack size 16 bytes, stdio.o(.text))

[Stack]

- Max Depth = 184
- Call Chain = _fflush ⇒ _writebuf ⇒ _sys_write ⇒ serial_init ⇒ mbed_assert_internal (Cycle)

[Calls]

- >> _writebuf

[Called By]

- >> _fclose_internal
- >> _do_fflush
- >> _deferredlazyseek
- >> __filbuf

_deferredlazyseek (Thumb, 60 bytes, Stack size 8 bytes, stdio.o(.text), UNUSED)

[Calls]

- >> _fflush

[Called By]

- >> __flsbuf
- >> __filbuf

_initio (Thumb, 210 bytes, Stack size 8 bytes, initio.o(.text))

[Stack]

- Max Depth = 560
- Call Chain = _initio ⇒ freopen ⇒ _sys_open ⇒ __0sscanf ⇒ __vfscanf_char ⇒ __vfscanf ⇒ _scanf_real ⇒ _scanf_really_real ⇒ _fp_value ⇒ _btod_etento ⇒ _btod_emul ⇒ _e2e

[Calls]

- >> __aeabi_memclr4
- >> freopen
- >> setvbuf
- >> __rt_SIGRTRED

[Called By]

- >> __rt_lib_init_stdio_2

_terminateio (Thumb, 56 bytes, Stack size 16 bytes, initio.o(.text), UNUSED)

[Calls]

- >> free
- >> _fclose_internal

__cxa_finalize (Thumb, 66 bytes, Stack size 24 bytes, cxa_finalize.o(.text), UNUSED)

[Calls]

- >> free
- >> __rt_ddtor_pointer_addr

__rt_SIGPVFN (Thumb, 14 bytes, Stack size 8 bytes, defsig_pvfn_outer.o(.text))

[Stack]

- Max Depth = 40
- Call Chain = __rt_SIGPVFN ⇒ __rt_SIGPVFN_inner ⇒ __default_signal_display ⇒ _ttywrch

[Calls]

- >> __rt_SIGPVFN_inner
- >> __sig_exit

[Called By]

- >> __cxa_pure_virtual

_localtime_r (Thumb, 178 bytes, Stack size 16 bytes, localtime_internal.o(.text))

[Stack]

- Max Depth = 20
- Call Chain = _localtime_r ⇒ __aeabi_memclr4

[Calls]

- >> __aeabi_memclr4

[Called By]

- >> localtime

_n$localtime_r (Thumb, 0 bytes, Stack size 16 bytes, localtime_internal.o(.text), UNUSED)

__default_new_handler() (Thumb, 4 bytes, Stack size 0 bytes, arm_newhandler_noexceptions.o(.text))

[Stack]

- Max Depth = 80
- Call Chain = __default_new_handler() ⇒ std::terminate() ⇒ __cxa_get_globals ⇒ __ARM_exceptions_buffer_init ⇒ malloc ⇒ __Heap_Full ⇒ __Heap_ProvideMemory ⇒ free

[Calls]

- >> std::terminate()

[Address Reference Count : 1]

- new.o(i._Znwj)

__aeabi_errno_addr (Thumb, 8 bytes, Stack size 0 bytes, rt_errno_addr.o(.text))

[Called By]

- >> __set_errno
- >> __read_errno
- >> _ftell_internal
- >> _fp_value

__errno (Thumb, 0 bytes, Stack size 0 bytes, rt_errno_addr.o(.text), UNUSED)

__rt_errno_addr (Thumb, 0 bytes, Stack size 0 bytes, rt_errno_addr.o(.text), UNUSED)

__Heap_ProvideMemory (Thumb, 52 bytes, Stack size 0 bytes, h1_extend.o(.text))

[Stack]

- Max Depth = 16
- Call Chain = __Heap_ProvideMemory ⇒ free

[Calls]

- >> free

[Called By]

- >> _init_alloc
- >> __Heap_Full

_ll_udiv10 (Thumb, 138 bytes, Stack size 12 bytes, lludiv10.o(.text))

[Stack]

- Max Depth = 12
- Call Chain = _ll_udiv10

[Called By]

- >> _printf_longlong_dec
- >> _fp_digits

isspace (Thumb, 18 bytes, Stack size 8 bytes, isspace.o(.text))

[Stack]

- Max Depth = 16
- Call Chain = isspace ⇒ __rt_ctype_table

[Calls]

- >> __rt_ctype_table

[Address Reference Count : 1]

- scanf_char.o(.text)

__lib_sel_fp_printf (Thumb, 2 bytes, Stack size 0 bytes, _printf_fp_dec.o(.text), UNUSED)

_printf_fp_dec_real (Thumb, 620 bytes, Stack size 104 bytes, _printf_fp_dec.o(.text))

[Stack]

- Max Depth = 320
- Call Chain = _printf_fp_dec_real ⇒ _fp_digits ⇒ _btod_etento ⇒ _btod_emul ⇒ _e2e

[Calls]

- >> _printf_post_padding
- >> _printf_pre_padding
- >> _printf_fp_infnan
- >> __rt_locale
- >> _fp_digits
- >> __ARM_fpclassify

[Called By]

- >> _printf_fp_dec

_printf_fp_hex_real (Thumb, 756 bytes, Stack size 72 bytes, _printf_fp_hex.o(.text))

[Stack]

- Max Depth = 112
- Call Chain = _printf_fp_hex_real ⇒ _printf_fp_infnan ⇒ _printf_post_padding

[Calls]

- >> _printf_post_padding
- >> _printf_pre_padding
- >> _printf_fp_infnan
- >> __ARM_fpclassify

[Called By]

- >> _printf_fp_hex

_printf_lcs_common (Thumb, 20 bytes, Stack size 8 bytes, _printf_wchar.o(.text))

[Stack]

- Max Depth = 88
- Call Chain = _printf_lcs_common ⇒ _printf_wctomb ⇒ _wcrtomb ⇒ __rt_ctype_table

[Calls]

- >> _printf_wctomb

[Called By]

- >> _printf_wstring
- >> _printf_wchar

_printf_wchar (Thumb, 16 bytes, Stack size 0 bytes, _printf_wchar.o(.text))

[Stack]

- Max Depth = 88
- Call Chain = _printf_wchar ⇒ _printf_lcs_common ⇒ _printf_wctomb ⇒ _wcrtomb ⇒ __rt_ctype_table

[Calls]

- >> _printf_lcs_common

[Called By]

- >> _printf_lc

_printf_wstring (Thumb, 8 bytes, Stack size 0 bytes, _printf_wchar.o(.text))

[Stack]

- Max Depth = 88
- Call Chain = _printf_wstring ⇒ _printf_lcs_common ⇒ _printf_wctomb ⇒ _wcrtomb ⇒ __rt_ctype_table

[Calls]

- >> _printf_lcs_common

[Called By]

- >> _printf_ls

__vfscanf (Thumb, 878 bytes, Stack size 96 bytes, _scanf.o(.text))

[Stack]

- Max Depth = 424
- Call Chain = __vfscanf ⇒ _scanf_real ⇒ _scanf_really_real ⇒ _fp_value ⇒ _btod_etento ⇒ _btod_emul ⇒ _e2e

[Calls]

- >> _scanf_string
- >> _scanf_int
- >> _scanf_real
- >> _scanf_wstring
- >> _scanf_wctomb
- >> _scanf_mbtowc
- >> _scanf_longlong

[Called By]

- >> __vfscanf_char

_scanf_really_real (Thumb, 668 bytes, Stack size 120 bytes, scanf_fp.o(.text))

[Stack]

- Max Depth = 328
- Call Chain = _scanf_really_real ⇒ _fp_value ⇒ _btod_etento ⇒ _btod_emul ⇒ _e2e

[Calls]

- >> _is_digit
- >> __rt_locale
- >> _fp_value
- >> __mathlib_narrow
- >> _scanf_infnan
- >> _scanf_hex_real

[Called By]

- >> _scanf_real

_scanf_wcharmap (Thumb, 30 bytes, Stack size 8 bytes, _scanf_wcharmap.o(.text))

[Stack]

- Max Depth = 8
- Call Chain = _scanf_wcharmap

[Called By]

- >> _scanf_wstring
- >> _scanf_wctomb

___backspace$unlocked (Thumb, 2 bytes, Stack size 0 bytes, backspace.o(.text), UNUSED)

__backspace (Thumb, 70 bytes, Stack size 8 bytes, backspace.o(.text))

[Stack]

- Max Depth = 8
- Call Chain = __backspace

[Calls]

- >> _ungetc_internal

[Address Reference Count : 1]

- scanf_char_file.o(.text)

_ftell_internal (Thumb, 66 bytes, Stack size 8 bytes, ftell.o(.text))

[Stack]

- Max Depth = 8
- Call Chain = _ftell_internal

[Calls]

- >> __aeabi_errno_addr

[Called By]

- >> _fseek

ftell (Thumb, 0 bytes, Stack size 8 bytes, ftell.o(.text), UNUSED)

_flushlinebuffered (Thumb, 50 bytes, Stack size 16 bytes, flushlinebuffered.o(.text), UNUSED)

[Calls]

- >> _do_fflush

[Called By]

- >> __filbuf

_mbrtowc (Thumb, 60 bytes, Stack size 16 bytes, _mbrtowc.o(.text))

[Stack]

- Max Depth = 24
- Call Chain = _mbrtowc ⇒ __rt_ctype_table

[Calls]

- >> __rt_ctype_table

[Called By]

- >> _scanf_mbtowc

_wcrtomb (Thumb, 64 bytes, Stack size 16 bytes, _wcrtomb.o(.text))

[Stack]

- Max Depth = 24
- Call Chain = _wcrtomb ⇒ __rt_ctype_table

[Calls]

- >> __rt_ctype_table

[Called By]

- >> _printf_wctomb
- >> _scanf_wctomb

__sig_exit (Thumb, 10 bytes, Stack size 0 bytes, defsig_exit.o(.text))

[Calls]

- >> _sys_exit

[Called By]

- >> __rt_SIGRTMEM
- >> __rt_SIGRTRED
- >> __rt_SIGPVFN
- >> __rt_SIGABRT

__rt_SIGRTRED (Thumb, 14 bytes, Stack size 8 bytes, defsig_rtred_outer.o(.text))

[Stack]

- Max Depth = 40
- Call Chain = __rt_SIGRTRED ⇒ __rt_SIGRTRED_inner ⇒ __default_signal_display ⇒ _ttywrch

[Calls]

- >> __sig_exit
- >> __rt_SIGRTRED_inner

[Called By]

- >> _initio

__rt_SIGRTMEM (Thumb, 14 bytes, Stack size 8 bytes, defsig_rtmem_outer.o(.text))

[Stack]

- Max Depth = 40
- Call Chain = __rt_SIGRTMEM ⇒ __rt_SIGRTMEM_inner ⇒ __default_signal_display ⇒ _ttywrch

[Calls]

- >> __sig_exit
- >> __rt_SIGRTMEM_inner

[Called By]

- >> _init_alloc
- >> __Heap_Broken

__rt_SIGPVFN_inner (Thumb, 14 bytes, Stack size 8 bytes, defsig_pvfn_inner.o(.text))

[Stack]

- Max Depth = 32
- Call Chain = __rt_SIGPVFN_inner ⇒ __default_signal_display ⇒ _ttywrch

[Calls]

- >> __default_signal_display

[Called By]

- >> __rt_SIGPVFN

__rt_heap_escrow (Thumb, 22 bytes, Stack size 0 bytes, heapauxa.o(.text))

[Called By]

- >> _init_alloc

__rt_heap_expand (Thumb, 52 bytes, Stack size 12 bytes, heapauxa.o(.text))

[Stack]

- Max Depth = 12
- Call Chain = __rt_heap_expand

[Called By]

- >> _init_alloc
- >> __Heap_Full

std::terminate() (Thumb, 26 bytes, Stack size 8 bytes, arm_exceptions_terminate.o(.text))

[Stack]

- Max Depth = 80
- Call Chain = std::terminate() ⇒ __cxa_get_globals ⇒ __ARM_exceptions_buffer_init ⇒ malloc ⇒ __Heap_Full ⇒ __Heap_ProvideMemory ⇒ free

[Calls]

- >> __cxa_get_globals
- >> abort

[Called By]

- >> __default_new_handler()

__cxa_get_globals (Thumb, 62 bytes, Stack size 16 bytes, arm_exceptions_globs.o(.text))

[Stack]

- Max Depth = 72
- Call Chain = __cxa_get_globals ⇒ __ARM_exceptions_buffer_init ⇒ malloc ⇒ __Heap_Full ⇒ __Heap_ProvideMemory ⇒ free

[Calls]

- >> malloc
- >> __rt_eh_globals_addr
- >> __ARM_exceptions_buffer_init
- >> abort

[Called By]

- >> std::terminate()

_sys_exit (Thumb, 8 bytes, Stack size 0 bytes, sys_exit.o(.text))

[Called By]

- >> __sig_exit
- >> abort

__rt_ctype_table (Thumb, 16 bytes, Stack size 8 bytes, rt_ctype_table.o(.text))

[Stack]

- Max Depth = 8
- Call Chain = __rt_ctype_table

[Calls]

- >> __rt_locale

[Called By]

- >> _wcrtomb
- >> _mbrtowc
- >> isspace

__rt_locale (Thumb, 8 bytes, Stack size 0 bytes, rt_locale.o(.text))

[Called By]

- >> __rt_ctype_table
- >> _scanf_really_real
- >> _printf_fp_dec_real
- >> __rt_lib_init_lc_common

__rt_eh_globals_addr (Thumb, 8 bytes, Stack size 0 bytes, rt_eh_globals_addr.o(.text))

[Called By]

- >> __cxa_get_globals

_printf_fp_infnan (Thumb, 112 bytes, Stack size 24 bytes, _printf_fp_infnan.o(.text))

[Stack]

- Max Depth = 40
- Call Chain = _printf_fp_infnan ⇒ _printf_post_padding

[Calls]

- >> _printf_post_padding
- >> _printf_pre_padding

[Called By]

- >> _printf_fp_hex_real
- >> _printf_fp_dec_real

_btod_etento (Thumb, 216 bytes, Stack size 72 bytes, bigflt0.o(.text))

[Stack]

- Max Depth = 120
- Call Chain = _btod_etento ⇒ _btod_emul ⇒ _e2e

[Calls]

- >> _btod_emul
- >> _btod_ediv

[Called By]

- >> _fp_value
- >> _fp_digits

_ungetc_internal (Thumb, 60 bytes, Stack size 0 bytes, ungetc.o(.text))

[Called By]

- >> __backspace

ungetc (Thumb, 0 bytes, Stack size 0 bytes, ungetc.o(.text), UNUSED)

abort (Thumb, 22 bytes, Stack size 8 bytes, abort.o(.text))

[Stack]

- Max Depth = 48
- Call Chain = abort ⇒ __rt_SIGABRT ⇒ __rt_SIGABRT_inner ⇒ __default_signal_display ⇒ _ttywrch

[Calls]

- >> _sys_exit
- >> __rt_SIGABRT

[Called By]

- >> __cxa_get_globals
- >> [local to arm_exceptions_c]::__default_terminate_handler()
- >> std::terminate()

__default_signal_display (Thumb, 50 bytes, Stack size 16 bytes, defsig_general.o(.text))

[Stack]

- Max Depth = 24
- Call Chain = __default_signal_display ⇒ _ttywrch

[Calls]

- >> _ttywrch

[Called By]

- >> __rt_SIGPVFN_inner
- >> __rt_SIGABRT_inner
- >> __rt_SIGRTMEM_inner
- >> __rt_SIGRTRED_inner

__rt_SIGRTRED_inner (Thumb, 14 bytes, Stack size 8 bytes, defsig_rtred_inner.o(.text))

[Stack]

- Max Depth = 32
- Call Chain = __rt_SIGRTRED_inner ⇒ __default_signal_display ⇒ _ttywrch

[Calls]

- >> __default_signal_display

[Called By]

- >> __rt_SIGRTRED

__rt_SIGRTMEM_inner (Thumb, 22 bytes, Stack size 8 bytes, defsig_rtmem_inner.o(.text))

[Stack]

- Max Depth = 32
- Call Chain = __rt_SIGRTMEM_inner ⇒ __default_signal_display ⇒ _ttywrch

[Calls]

- >> __default_signal_display

[Called By]

- >> __rt_SIGRTMEM

__ARM_exceptions_buffer_init (Thumb, 18 bytes, Stack size 8 bytes, arm_exceptions_mem.o(.text))

[Stack]

- Max Depth = 56
- Call Chain = __ARM_exceptions_buffer_init ⇒ malloc ⇒ __Heap_Full ⇒ __Heap_ProvideMemory ⇒ free

[Calls]

- >> malloc

[Called By]

- >> __cxa_get_globals

__ARM_exceptions_buffer_allocate (Thumb, 22 bytes, Stack size 0 bytes, arm_exceptions_mem.o(.text), UNUSED)

__ARM_exceptions_buffer_free (Thumb, 20 bytes, Stack size 0 bytes, arm_exceptions_mem.o(.text), UNUSED)

_ttywrch (Thumb, 14 bytes, Stack size 8 bytes, sys_wrch.o(.text))

[Stack]

- Max Depth = 8
- Call Chain = _ttywrch

[Called By]

- >> __default_signal_display

__I$use$semihosting (Thumb, 0 bytes, Stack size 0 bytes, use_no_semi.o(.text), UNUSED)

__use_no_semihosting_swi (Thumb, 2 bytes, Stack size 0 bytes, use_no_semi.o(.text), UNUSED)

__semihosting_library_function (Thumb, 0 bytes, Stack size 80 bytes, indicate_semi.o(.text), UNUSED)

_scanf_really_hex_real (Thumb, 786 bytes, Stack size 80 bytes, scanf_hexfp.o(.text))

[Stack]

- Max Depth = 176
- Call Chain = _scanf_really_hex_real ⇒ __support_ldexp ⇒ __hardfp_ldexp ⇒ __mathlib_dbl_underflow ⇒ __aeabi_dmul

[Calls]

- >> _chval
- >> __support_ldexp
- >> __aeabi_llsl
- >> __mathlib_narrow

[Called By]

- >> _scanf_hex_real

_scanf_really_infnan (Thumb, 292 bytes, Stack size 72 bytes, scanf_infnan.o(.text))

[Stack]

- Max Depth = 72
- Call Chain = _scanf_really_infnan

[Called By]

- >> _scanf_infnan

__rt_SIGABRT (Thumb, 14 bytes, Stack size 8 bytes, defsig_abrt_outer.o(.text))

[Stack]

- Max Depth = 40
- Call Chain = __rt_SIGABRT ⇒ __rt_SIGABRT_inner ⇒ __default_signal_display ⇒ _ttywrch

[Calls]

- >> __sig_exit
- >> __rt_SIGABRT_inner

[Called By]

- >> abort

__aeabi_llsl (Thumb, 0 bytes, Stack size 0 bytes, llshl.o(.text))

[Called By]

- >> _scanf_really_hex_real

_ll_shift_l (Thumb, 38 bytes, Stack size 0 bytes, llshl.o(.text), UNUSED)

__rt_SIGABRT_inner (Thumb, 14 bytes, Stack size 8 bytes, defsig_abrt_inner.o(.text))

[Stack]

- Max Depth = 32
- Call Chain = __rt_SIGABRT_inner ⇒ __default_signal_display ⇒ _ttywrch

[Calls]

- >> __default_signal_display

[Called By]

- >> __rt_SIGABRT

_btod_d2e (Thumb, 62 bytes, Stack size 0 bytes, btod.o(CL$$btod_d2e))

[Calls]

- >> _d2e_norm_op1

[Called By]

- >> _fp_digits

_d2e_denorm_low (Thumb, 70 bytes, Stack size 0 bytes, btod.o(CL$$btod_d2e_denorm_low))

[Called By]

- >> _d2e_norm_op1

_d2e_norm_op1 (Thumb, 96 bytes, Stack size 0 bytes, btod.o(CL$$btod_d2e_norm_op1))

[Calls]

- >> _d2e_denorm_low

[Called By]

- >> _btod_d2e

__btod_div_common (Thumb, 696 bytes, Stack size 24 bytes, btod.o(CL$$btod_div_common))

[Stack]

- Max Depth = 24
- Call Chain = __btod_div_common

[Called By]

- >> _btod_edivd
- >> _btod_ediv

_e2d (Thumb, 80 bytes, Stack size 8 bytes, btod.o(CL$$btod_e2d))

[Stack]

- Max Depth = 32
- Call Chain = _e2d ⇒ _e2e

[Calls]

- >> _e2e

[Called By]

- >> _btod_emuld
- >> _btod_edivd

_e2e (Thumb, 198 bytes, Stack size 24 bytes, btod.o(CL$$btod_e2e))

[Stack]

- Max Depth = 24
- Call Chain = _e2e

[Called By]

- >> _btod_emul
- >> _btod_ediv
- >> _e2d

_btod_ediv (Thumb, 40 bytes, Stack size 24 bytes, btod.o(CL$$btod_ediv))

[Stack]

- Max Depth = 48
- Call Chain = _btod_ediv ⇒ _e2e

[Calls]

- >> _e2e
- >> __btod_div_common

[Called By]

- >> _btod_etento
- >> _fp_digits

_btod_edivd (Thumb, 40 bytes, Stack size 24 bytes, btod.o(CL$$btod_edivd))

[Stack]

- Max Depth = 56
- Call Chain = _btod_edivd ⇒ _e2d ⇒ _e2e

[Calls]

- >> _e2d
- >> __btod_div_common

[Called By]

- >> _fp_value

_btod_emul (Thumb, 40 bytes, Stack size 24 bytes, btod.o(CL$$btod_emul))

[Stack]

- Max Depth = 48
- Call Chain = _btod_emul ⇒ _e2e

[Calls]

- >> __btod_mult_common
- >> _e2e

[Called By]

- >> _btod_etento
- >> _fp_digits

_btod_emuld (Thumb, 40 bytes, Stack size 24 bytes, btod.o(CL$$btod_emuld))

[Stack]

- Max Depth = 56
- Call Chain = _btod_emuld ⇒ _e2d ⇒ _e2e

[Calls]

- >> __btod_mult_common
- >> _e2d

[Called By]

- >> _fp_value

__btod_mult_common (Thumb, 580 bytes, Stack size 16 bytes, btod.o(CL$$btod_mult_common))

[Stack]

- Max Depth = 16
- Call Chain = __btod_mult_common

[Called By]

- >> _btod_emuld
- >> _btod_emul

main (Thumb, 18 bytes, Stack size 8 bytes, retarget.o(i.$Sub$$main))

[Stack]

- Max Depth = 592 + Unknown Stack Size
- Call Chain = main ⇒ $Super$$main ⇒ mbed::Stream::scanf(const char*, ...) ⇒ vfscanf ⇒ __vfscanf_char_file ⇒ __vfscanf_char ⇒ __vfscanf ⇒ _scanf_real ⇒ _scanf_really_real ⇒ _fp_value ⇒ _btod_etento ⇒ _btod_emul ⇒ _e2e

[Calls]

- >> mbed_main
- >> $Super$$main
- >> mbed_sdk_init

[Called By]

- >> __rt_entry_main

HAL_ADC_ConfigChannel (Thumb, 422 bytes, Stack size 16 bytes, stm32f4xx_hal_adc.o(i.HAL_ADC_ConfigChannel))

[Stack]

- Max Depth = 16
- Call Chain = HAL_ADC_ConfigChannel

[Called By]

- >> adc_read

HAL_ADC_GetValue (Thumb, 6 bytes, Stack size 0 bytes, stm32f4xx_hal_adc.o(i.HAL_ADC_GetValue))

[Called By]

- >> adc_read

HAL_ADC_Init (Thumb, 346 bytes, Stack size 16 bytes, stm32f4xx_hal_adc.o(i.HAL_ADC_Init))

[Stack]

- Max Depth = 16
- Call Chain = HAL_ADC_Init

[Calls]

- >> HAL_ADC_MspInit

[Called By]

- >> analogin_init

HAL_ADC_MspInit (Thumb, 2 bytes, Stack size 0 bytes, stm32f4xx_hal_adc.o(i.HAL_ADC_MspInit))

[Called By]

- >> HAL_ADC_Init

HAL_ADC_PollForConversion (Thumb, 128 bytes, Stack size 24 bytes, stm32f4xx_hal_adc.o(i.HAL_ADC_PollForConversion))

[Stack]

- Max Depth = 24
- Call Chain = HAL_ADC_PollForConversion

[Calls]

- >> HAL_GetTick

[Called By]

- >> adc_read

HAL_ADC_Start (Thumb, 198 bytes, Stack size 8 bytes, stm32f4xx_hal_adc.o(i.HAL_ADC_Start))

[Stack]

- Max Depth = 8
- Call Chain = HAL_ADC_Start

[Called By]

- >> adc_read

HAL_GPIO_Init (Thumb, 494 bytes, Stack size 40 bytes, stm32f4xx_hal_gpio.o(i.HAL_GPIO_Init))

[Stack]

- Max Depth = 40
- Call Chain = HAL_GPIO_Init

[Called By]

- >> pin_function

HAL_GetTick (Thumb, 6 bytes, Stack size 0 bytes, stm32f4xx_hal.o(i.HAL_GetTick))

[Called By]

- >> HAL_ADC_PollForConversion
- >> HAL_RTC_SetTime
- >> HAL_RTC_SetDate
- >> HAL_RTC_Init
- >> HAL_RCC_OscConfig
- >> HAL_RCC_ClockConfig

HAL_I2C_Init (Thumb, 248 bytes, Stack size 16 bytes, stm32f4xx_hal_i2c.o(i.HAL_I2C_Init))

[Stack]

- Max Depth = 28
- Call Chain = HAL_I2C_Init ⇒ HAL_RCC_GetPCLK1Freq ⇒ HAL_RCC_GetSysClockFreq

[Calls]

- >> HAL_I2C_MspInit
- >> HAL_RCC_GetPCLK1Freq

[Called By]

- >> i2c_init
- >> i2c_frequency

HAL_I2C_MspInit (Thumb, 2 bytes, Stack size 0 bytes, stm32f4xx_hal_i2c.o(i.HAL_I2C_MspInit))

[Called By]

- >> HAL_I2C_Init

HAL_IncTick (Thumb, 10 bytes, Stack size 0 bytes, stm32f4xx_hal.o(i.HAL_IncTick))

[Called By]

- >> timer_irq_handler

HAL_Init (Thumb, 48 bytes, Stack size 8 bytes, stm32f4xx_hal.o(i.HAL_Init))

[Stack]

- Max Depth = 56
- Call Chain = HAL_Init ⇒ HAL_InitTick ⇒ NVIC_SetVector ⇒ __aeabi_memcpy4

[Calls]

- >> HAL_MspInit
- >> HAL_NVIC_SetPriorityGrouping
- >> HAL_InitTick

[Called By]

- >> SystemInit
- >> mbed_sdk_init

HAL_InitTick (Thumb, 144 bytes, Stack size 16 bytes, hal_tick.o(i.HAL_InitTick))

[Stack]

- Max Depth = 48
- Call Chain = HAL_InitTick ⇒ NVIC_SetVector ⇒ __aeabi_memcpy4

[Calls]

- >> SystemCoreClockUpdate
- >> HAL_TIM_OC_Start
- >> HAL_TIM_OC_Init
- >> NVIC_SetVector

[Called By]

- >> us_ticker_read
- >> HAL_Init
- >> HAL_RCC_ClockConfig
- >> us_ticker_init

HAL_MspInit (Thumb, 2 bytes, Stack size 0 bytes, stm32f4xx_hal_msp_template.o(i.HAL_MspInit))

[Called By]

- >> HAL_Init

HAL_NVIC_SetPriorityGrouping (Thumb, 30 bytes, Stack size 0 bytes, stm32f4xx_hal_cortex.o(i.HAL_NVIC_SetPriorityGrouping))

[Called By]

- >> HAL_Init

HAL_RCC_ClockConfig (Thumb, 546 bytes, Stack size 32 bytes, stm32f4xx_hal_rcc.o(i.HAL_RCC_ClockConfig))

[Stack]

- Max Depth = 80
- Call Chain = HAL_RCC_ClockConfig ⇒ HAL_InitTick ⇒ NVIC_SetVector ⇒ __aeabi_memcpy4

[Calls]

- >> HAL_GetTick
- >> HAL_InitTick

[Called By]

- >> SystemInit
- >> SetSysClock_PLL_HSE

HAL_RCC_GetPCLK1Freq (Thumb, 64 bytes, Stack size 8 bytes, stm32f4xx_hal_rcc.o(i.HAL_RCC_GetPCLK1Freq))

[Stack]

- Max Depth = 12
- Call Chain = HAL_RCC_GetPCLK1Freq ⇒ HAL_RCC_GetSysClockFreq

[Calls]

- >> HAL_RCC_GetSysClockFreq

[Called By]

- >> HAL_I2C_Init
- >> UART_SetConfig

HAL_RCC_GetPCLK2Freq (Thumb, 64 bytes, Stack size 8 bytes, stm32f4xx_hal_rcc.o(i.HAL_RCC_GetPCLK2Freq))

[Stack]

- Max Depth = 12
- Call Chain = HAL_RCC_GetPCLK2Freq ⇒ HAL_RCC_GetSysClockFreq

[Calls]

- >> HAL_RCC_GetSysClockFreq

[Called By]

- >> UART_SetConfig

HAL_RCC_GetSysClockFreq (Thumb, 132 bytes, Stack size 4 bytes, stm32f4xx_hal_rcc.o(i.HAL_RCC_GetSysClockFreq))

[Stack]

- Max Depth = 4
- Call Chain = HAL_RCC_GetSysClockFreq

[Called By]

- >> HAL_RCC_GetPCLK2Freq
- >> HAL_RCC_GetPCLK1Freq

HAL_RCC_OscConfig (Thumb, 868 bytes, Stack size 40 bytes, stm32f4xx_hal_rcc.o(i.HAL_RCC_OscConfig))

[Stack]

- Max Depth = 40
- Call Chain = HAL_RCC_OscConfig

[Calls]

- >> HAL_GetTick

[Called By]

- >> SystemInit
- >> SetSysClock_PLL_HSE
- >> rtc_init

HAL_RTC_GetDate (Thumb, 98 bytes, Stack size 4 bytes, stm32f4xx_hal_rtc.o(i.HAL_RTC_GetDate))

[Stack]

- Max Depth = 4
- Call Chain = HAL_RTC_GetDate

[Called By]

- >> rtc_read

HAL_RTC_GetTime (Thumb, 114 bytes, Stack size 8 bytes, stm32f4xx_hal_rtc.o(i.HAL_RTC_GetTime))

[Stack]

- Max Depth = 8
- Call Chain = HAL_RTC_GetTime

[Called By]

- >> rtc_read

HAL_RTC_Init (Thumb, 204 bytes, Stack size 16 bytes, stm32f4xx_hal_rtc.o(i.HAL_RTC_Init))

[Stack]

- Max Depth = 16
- Call Chain = HAL_RTC_Init

[Calls]

- >> HAL_GetTick
- >> HAL_RTC_MspInit

[Called By]

- >> rtc_init

HAL_RTC_MspInit (Thumb, 2 bytes, Stack size 0 bytes, stm32f4xx_hal_rtc.o(i.HAL_RTC_MspInit))

[Called By]

- >> HAL_RTC_Init

HAL_RTC_SetDate (Thumb, 298 bytes, Stack size 32 bytes, stm32f4xx_hal_rtc.o(i.HAL_RTC_SetDate))

[Stack]

- Max Depth = 32
- Call Chain = HAL_RTC_SetDate

[Calls]

- >> HAL_GetTick
- >> RTC_ByteToBcd2

[Called By]

- >> rtc_write

HAL_RTC_SetTime (Thumb, 322 bytes, Stack size 40 bytes, stm32f4xx_hal_rtc.o(i.HAL_RTC_SetTime))

[Stack]

- Max Depth = 40
- Call Chain = HAL_RTC_SetTime

[Calls]

- >> HAL_GetTick
- >> RTC_ByteToBcd2

[Called By]

- >> rtc_write

HAL_TIM_OC_Init (Thumb, 54 bytes, Stack size 8 bytes, stm32f4xx_hal_tim.o(i.HAL_TIM_OC_Init))

[Stack]

- Max Depth = 20
- Call Chain = HAL_TIM_OC_Init ⇒ TIM_Base_SetConfig

[Calls]

- >> TIM_Base_SetConfig
- >> HAL_TIM_OC_MspInit

[Called By]

- >> HAL_InitTick

HAL_TIM_OC_MspInit (Thumb, 2 bytes, Stack size 0 bytes, stm32f4xx_hal_tim.o(i.HAL_TIM_OC_MspInit))

[Called By]

- >> HAL_TIM_OC_Init

HAL_TIM_OC_Start (Thumb, 54 bytes, Stack size 0 bytes, stm32f4xx_hal_tim.o(i.HAL_TIM_OC_Start))

[Called By]

- >> HAL_InitTick

HAL_UART_Init (Thumb, 94 bytes, Stack size 16 bytes, stm32f4xx_hal_uart.o(i.HAL_UART_Init))

[Stack]

- Max Depth = 52
- Call Chain = HAL_UART_Init ⇒ UART_SetConfig ⇒ HAL_RCC_GetPCLK2Freq ⇒ HAL_RCC_GetSysClockFreq

[Calls]

- >> HAL_UART_MspInit
- >> UART_SetConfig

[Called By]

- >> serial_init
- >> serial_format
- >> serial_baud

HAL_UART_MspInit (Thumb, 2 bytes, Stack size 0 bytes, stm32f4xx_hal_uart.o(i.HAL_UART_MspInit))

[Called By]

- >> HAL_UART_Init

NVIC_SetVector (Thumb, 48 bytes, Stack size 24 bytes, cmsis_nvic.o(i.NVIC_SetVector))

[Stack]

- Max Depth = 32
- Call Chain = NVIC_SetVector ⇒ __aeabi_memcpy4

[Calls]

- >> __aeabi_memcpy4

[Called By]

- >> serial_irq_set
- >> HAL_InitTick
- >> gpio_irq_init

RTC_ByteToBcd2 (Thumb, 48 bytes, Stack size 0 bytes, stm32f4xx_hal_rtc.o(i.RTC_ByteToBcd2))

[Called By]

- >> HAL_RTC_SetTime
- >> HAL_RTC_SetDate

SetSysClock_PLL_HSE (Thumb, 132 bytes, Stack size 80 bytes, system_stm32f4xx.o(i.SetSysClock_PLL_HSE))

[Stack]

- Max Depth = 160
- Call Chain = SetSysClock_PLL_HSE ⇒ HAL_RCC_ClockConfig ⇒ HAL_InitTick ⇒ NVIC_SetVector ⇒ __aeabi_memcpy4

[Calls]

- >> HAL_RCC_OscConfig
- >> HAL_RCC_ClockConfig

[Called By]

- >> SystemInit

Set_GPIO_Clock (Thumb, 142 bytes, Stack size 16 bytes, pinmap.o(i.Set_GPIO_Clock))

[Stack]

- Max Depth = 16 + In Cycle
- Call Chain = Set_GPIO_Clock ⇒ error (Cycle)

[Calls]

- >> error

[Called By]

- >> gpio_irq_init
- >> pin_mode
- >> pin_function
- >> gpio_init

SystemCoreClockUpdate (Thumb, 112 bytes, Stack size 8 bytes, system_stm32f4xx.o(i.SystemCoreClockUpdate))

[Stack]

- Max Depth = 8
- Call Chain = SystemCoreClockUpdate

[Called By]

- >> mbed_sdk_init
- >> HAL_InitTick

SystemInit (Thumb, 226 bytes, Stack size 88 bytes, system_stm32f4xx.o(i.SystemInit))

[Stack]

- Max Depth = 248
- Call Chain = SystemInit ⇒ SetSysClock_PLL_HSE ⇒ HAL_RCC_ClockConfig ⇒ HAL_InitTick ⇒ NVIC_SetVector ⇒ __aeabi_memcpy4

[Calls]

- >> HAL_Init
- >> HAL_RCC_OscConfig
- >> HAL_RCC_ClockConfig
- >> SetSysClock_PLL_HSE

[Address Reference Count : 1]

- startup_stm32f401xe.o(.text)

TIM_Base_SetConfig (Thumb, 132 bytes, Stack size 12 bytes, stm32f4xx_hal_tim.o(i.TIM_Base_SetConfig))

[Stack]

- Max Depth = 12
- Call Chain = TIM_Base_SetConfig

[Called By]

- >> HAL_TIM_OC_Init

startMillis() (Thumb, 18 bytes, Stack size 0 bytes, millis.o(i._Z11startMillisv))

[Stack]

- Max Depth = 32
- Call Chain = startMillis() ⇒ mbed::Ticker::setup(unsigned) ⇒ mbed::TimerEvent::insert(unsigned) ⇒ ticker_insert_event

[Calls]

- >> mbed::Ticker::setup(unsigned)

[Called By]

- >> $Super$$main

millisTicker() (Thumb, 10 bytes, Stack size 0 bytes, millis.o(i._Z12millisTickerv))
[Address Reference Count : 1]

- millis.o(i._Z11startMillisv)

update_modbus() (Thumb, 522 bytes, Stack size 16 bytes, main.o(i._Z13update_modbusv))

[Stack]

- Max Depth = 832 + Unknown Stack Size
- Call Chain = update_modbus() ⇒ ModbusSlave232::update(int*, unsigned) ⇒ ModbusSlave232::read_holding_registers(unsigned, unsigned char, int*) ⇒ mbed::Stream::putc(int) ⇒ fflush ⇒ _do_fflush ⇒ _fflush ⇒ _writebuf ⇒ _sys_write ⇒ serial_init ⇒ mbed_assert_internal (Cycle)

[Calls]

- >> mbed_assert_internal
- >> ModbusSlave232::update(int*, unsigned)

[Address Reference Count : 1]

- main.o(i.main)

millis() (Thumb, 6 bytes, Stack size 0 bytes, millis.o(i._Z6millisv))

[Called By]

- >> ModbusSlave232::update(int*, unsigned)

FlexTicker::handler() (Thumb, 28 bytes, Stack size 0 bytes, softserial.o(i._ZN10FlexTicker7handlerEv))
[Address Reference Count : 1]

- softserial.o(.constdata__ZTV10FlexTicker)

SoftSerial::prepare_tx(int) (Thumb, 192 bytes, Stack size 16 bytes, softserial_tx.o(i._ZN10SoftSerial10prepare_txEi))

[Stack]

- Max Depth = 16
- Call Chain = SoftSerial::prepare_tx(int)

[Called By]

- >> SoftSerial::_putc(int)

SoftSerial::rx_handler() (Thumb, 284 bytes, Stack size 16 bytes, softserial_rx.o(i._ZN10SoftSerial10rx_handlerEv))

[Stack]

- Max Depth = 264 + Unknown Stack Size
- Call Chain = SoftSerial::rx_handler() ⇒ mbed::InterruptIn::read() ⇒ mbed_assert_internal ⇒ error ⇒ exit ⇒ fflush ⇒ _do_fflush ⇒ _fflush ⇒ _writebuf ⇒ _sys_write ⇒ serial_init ⇒ mbed_assert_internal (Cycle)

[Calls]

- >> mbed::InterruptIn::read()
- >> mbed::TimerEvent::remove()
- >> mbed::TimerEvent::insert(unsigned)
- >> gpio_irq_set

[Address Reference Count : 1]

- softserial.o(.constdata)

SoftSerial::send_break() (Thumb, 116 bytes, Stack size 16 bytes, softserial_tx.o(i._ZN10SoftSerial10send_breakEv), UNUSED)

[Calls]

- >> wait_us
- >> mbed_assert_internal

SoftSerial::tx_handler() (Thumb, 248 bytes, Stack size 24 bytes, softserial_tx.o(i._ZN10SoftSerial10tx_handlerEv))

[Stack]

- Max Depth = 264 + Unknown Stack Size
- Call Chain = SoftSerial::tx_handler() ⇒ mbed_assert_internal ⇒ error ⇒ exit ⇒ fflush ⇒ _do_fflush ⇒ _fflush ⇒ _writebuf ⇒ _sys_write ⇒ serial_init ⇒ mbed_assert_internal (Cycle)

[Calls]

- >> mbed_assert_internal
- >> mbed::TimerEvent::insert(unsigned)

[Called By]

- >> SoftSerial::_putc(int)

[Address Reference Count : 1]

- softserial.o(.constdata)

SoftSerial::rx_gpio_irq_handler() (Thumb, 52 bytes, Stack size 8 bytes, softserial_rx.o(i._ZN10SoftSerial19rx_gpio_irq_handlerEv))

[Stack]

- Max Depth = 96
- Call Chain = SoftSerial::rx_gpio_irq_handler() ⇒ mbed::InterruptIn::fall(void(*)()) ⇒ gpio_irq_set ⇒ pin_function ⇒ mbed_assert_internal (Cycle)

[Calls]

- >> us_ticker_read
- >> mbed::InterruptIn::fall(void(*)())
- >> mbed::TimerEvent::insert(unsigned)

[Address Reference Count : 2]

- softserial_rx.o(.constdata)
- softserial.o(.constdata)

SoftSerial::baud(int) (Thumb, 10 bytes, Stack size 0 bytes, softserial.o(i._ZN10SoftSerial4baudEi))

[Called By]

- >> $Super$$main

SoftSerial::_getc() (Thumb, 18 bytes, Stack size 0 bytes, softserial_rx.o(i._ZN10SoftSerial5_getcEv))

[Calls]

- >> SoftSerial::_getc()

[Called By]

- >> SoftSerial::_getc()

[Address Reference Count : 1]

- softserial.o(.constdata__ZTV10SoftSerial)

SoftSerial::_putc(int) (Thumb, 52 bytes, Stack size 16 bytes, softserial_tx.o(i._ZN10SoftSerial5_putcEi))

[Stack]

- Max Depth = 280 + Unknown Stack Size
- Call Chain = SoftSerial::_putc(int) ⇒ SoftSerial::tx_handler() ⇒ mbed_assert_internal ⇒ error ⇒ exit ⇒ fflush ⇒ _do_fflush ⇒ _fflush ⇒ _writebuf ⇒ _sys_write ⇒ serial_init ⇒ mbed_assert_internal (Cycle)

[Calls]

- >> SoftSerial::prepare_tx(int)
- >> us_ticker_read
- >> SoftSerial::tx_handler()

[Address Reference Count : 1]

- softserial.o(.constdata__ZTV10SoftSerial)

SoftSerial::SoftSerial(PinName, PinName, const char*) (Thumb, 304 bytes, Stack size 40 bytes, softserial.o(i._ZN10SoftSerialC1E7PinNameS0_PKc))

[Stack]

- Max Depth = 640 + Unknown Stack Size
- Call Chain = SoftSerial::SoftSerial(PinName, PinName, const char*) ⇒ mbed::Stream::Stream__sub_object(const char*) ⇒ fopen ⇒ freopen ⇒ _sys_open ⇒ __0sscanf ⇒ __vfscanf_char ⇒ __vfscanf ⇒ _scanf_real ⇒ _scanf_really_real ⇒ _fp_value ⇒ _btod_etento ⇒ _btod_emul ⇒ _e2e

[Calls]

- >> gpio_init_out
- >> mbed_assert_internal
- >> gpio_irq_set
- >> mbed::Stream::Stream__sub_object(const char*)
- >> mbed::InterruptIn::InterruptIn(PinName)
- >> mbed::TimerEvent::TimerEvent__sub_object()
- >> __aeabi_vec_ctor_nocookie_nodtor
- >> operator new(unsigned)

[Called By]

- >> __sti___8_main_cpp_led1

SoftSerial::SoftSerial__sub_object(PinName, PinName, const char*) (Thumb, 0 bytes, Stack size 40 bytes, softserial.o(i._ZN10SoftSerialC1E7PinNameS0_PKc), UNUSED)

SoftSerial::~SoftSerial() (Thumb, 70 bytes, Stack size 8 bytes, softserial.o(i._ZN10SoftSerialD1Ev))

[Stack]

- Max Depth = 48
- Call Chain = SoftSerial::~SoftSerial() ⇒ mbed::Stream::~Stream__sub_object() ⇒ fclose

[Calls]

- >> mbed::Stream::~Stream__sub_object()
- >> mbed::TimerEvent::~TimerEvent__sub_object()
- >> operator delete (void*)

[Address Reference Count : 2]

- main.o(i.__sti___8_main_cpp_led1)
- softserial.o(.constdata__ZTV10SoftSerial)

SoftSerial::~SoftSerial__sub_object() (Thumb, 0 bytes, Stack size 8 bytes, softserial.o(i._ZN10SoftSerialD1Ev), UNUSED)

TSL2561_I2C::enablePower() (Thumb, 34 bytes, Stack size 16 bytes, tsl2561_i2c.o(i._ZN11TSL2561_I2C11enablePowerEv))

[Stack]

- Max Depth = 304 + Unknown Stack Size
- Call Chain = TSL2561_I2C::enablePower() ⇒ mbed::I2C::write(int, const char*, int, bool) ⇒ i2c_frequency ⇒ mbed_assert_internal ⇒ error ⇒ exit ⇒ fflush ⇒ _do_fflush ⇒ _fflush ⇒ _writebuf ⇒ _sys_write ⇒ serial_init ⇒ mbed_assert_internal (Cycle)

[Calls]

- >> mbed::I2C::write(int, const char*, int, bool)

[Called By]

- >> $Super$$main

TSL2561_I2C::readSingleRegister(char) (Thumb, 58 bytes, Stack size 24 bytes, tsl2561_i2c.o(i._ZN11TSL2561_I2C18readSingleRegisterEc))

[Stack]

- Max Depth = 312 + Unknown Stack Size
- Call Chain = TSL2561_I2C::readSingleRegister(char) ⇒ mbed::I2C::write(int, const char*, int, bool) ⇒ i2c_frequency ⇒ mbed_assert_internal ⇒ error ⇒ exit ⇒ fflush ⇒ _do_fflush ⇒ _fflush ⇒ _writebuf ⇒ _sys_write ⇒ serial_init ⇒ mbed_assert_internal (Cycle)

[Calls]

- >> mbed::I2C::write(int, const char*, int, bool)
- >> mbed::I2C::read(int, char*, int, bool)

[Called By]

- >> TSL2561_I2C::getLux()

TSL2561_I2C::getLux() (Thumb, 732 bytes, Stack size 80 bytes, tsl2561_i2c.o(i._ZN11TSL2561_I2C6getLuxEv))

[Stack]

- Max Depth = 392 + Unknown Stack Size
- Call Chain = TSL2561_I2C::getLux() ⇒ TSL2561_I2C::readSingleRegister(char) ⇒ mbed::I2C::write(int, const char*, int, bool) ⇒ i2c_frequency ⇒ mbed_assert_internal ⇒ error ⇒ exit ⇒ fflush ⇒ _do_fflush ⇒ _fflush ⇒ _writebuf ⇒ _sys_write ⇒ serial_init ⇒ mbed_assert_internal (Cycle)

[Calls]

- >> mbed::I2C::write(int, const char*, int, bool)
- >> mbed::I2C::read(int, char*, int, bool)
- >> TSL2561_I2C::readSingleRegister(char)
- >> __hardfp_pow
- >> __aeabi_f2d
- >> __aeabi_dmul
- >> __aeabi_cdcmple
- >> __aeabi_i2d
- >> __aeabi_ddiv
- >> __aeabi_dsub
- >> __aeabi_d2f

[Called By]

- >> $Super$$main

TSL2561_I2C::TSL2561_I2C(PinName, PinName) (Thumb, 50 bytes, Stack size 16 bytes, tsl2561_i2c.o(i._ZN11TSL2561_I2CC1E7PinNameS0_))

[Stack]

- Max Depth = 320 + Unknown Stack Size
- Call Chain = TSL2561_I2C::TSL2561_I2C(PinName, PinName) ⇒ mbed::I2C::I2C(PinName, PinName) ⇒ i2c_init ⇒ mbed_assert_internal ⇒ error ⇒ exit ⇒ fflush ⇒ _do_fflush ⇒ _fflush ⇒ _writebuf ⇒ _sys_write ⇒ serial_init ⇒ mbed_assert_internal (Cycle)

[Calls]

- >> mbed::I2C::I2C(PinName, PinName)
- >> mbed::I2C::frequency(int)
- >> mbed::I2C::write(int, const char*, int, bool)

[Called By]

- >> __sti___8_main_cpp_led1

TSL2561_I2C::TSL2561_I2C__sub_object(PinName, PinName) (Thumb, 0 bytes, Stack size 16 bytes, tsl2561_i2c.o(i._ZN11TSL2561_I2CC1E7PinNameS0_), UNUSED)

ModbusSlave232::read_holding_registers(unsigned, unsigned char, int*) (Thumb, 178 bytes, Stack size 280 bytes, modbusslave232.o(i._ZN14ModbusSlave23222read_holding_registersEjhPi))

[Stack]

- Max Depth = 512
- Call Chain = ModbusSlave232::read_holding_registers(unsigned, unsigned char, int*) ⇒ mbed::Stream::putc(int) ⇒ fflush ⇒ _do_fflush ⇒ _fflush ⇒ _writebuf ⇒ _sys_write ⇒ serial_init ⇒ mbed_assert_internal (Cycle)

[Calls]

- >> mbed::Stream::putc(int)
- >> ModbusSlave232::crc(unsigned char*, unsigned char, unsigned char)

[Called By]

- >> ModbusSlave232::update(int*, unsigned)

ModbusSlave232::preset_multiple_registers(unsigned, unsigned char, unsigned char*, int*) (Thumb, 174 bytes, Stack size 32 bytes, modbusslave232.o(i._ZN14ModbusSlave23225preset_multiple_registersEjhPhPi))

[Stack]

- Max Depth = 264
- Call Chain = ModbusSlave232::preset_multiple_registers(unsigned, unsigned char, unsigned char*, int*) ⇒ mbed::Stream::putc(int) ⇒ fflush ⇒ _do_fflush ⇒ _fflush ⇒ _writebuf ⇒ _sys_write ⇒ serial_init ⇒ mbed_assert_internal (Cycle)

[Calls]

- >> mbed::Stream::putc(int)
- >> ModbusSlave232::crc(unsigned char*, unsigned char, unsigned char)

[Called By]

- >> ModbusSlave232::update(int*, unsigned)

ModbusSlave232::crc(unsigned char*, unsigned char, unsigned char) (Thumb, 156 bytes, Stack size 4 bytes, modbusslave232.o(i._ZN14ModbusSlave2323crcEPhhh))

[Stack]

- Max Depth = 4
- Call Chain = ModbusSlave232::crc(unsigned char*, unsigned char, unsigned char)

[Called By]

- >> ModbusSlave232::update(int*, unsigned)
- >> ModbusSlave232::preset_multiple_registers(unsigned, unsigned char, unsigned char*, int*)
- >> ModbusSlave232::read_holding_registers(unsigned, unsigned char, int*)

ModbusSlave232::update(int*, unsigned) (Thumb, 528 bytes, Stack size 304 bytes, modbusslave232.o(i._ZN14ModbusSlave2326updateEPij))

[Stack]

- Max Depth = 816
- Call Chain = ModbusSlave232::update(int*, unsigned) ⇒ ModbusSlave232::read_holding_registers(unsigned, unsigned char, int*) ⇒ mbed::Stream::putc(int) ⇒ fflush ⇒ _do_fflush ⇒ _fflush ⇒ _writebuf ⇒ _sys_write ⇒ serial_init ⇒ mbed_assert_internal (Cycle)

[Calls]

- >> AjK::MODSERIAL::rxBufferEmpty()
- >> AjK::MODSERIAL::__getc(bool)
- >> mbed::Stream::putc(int)
- >> millis()
- >> ModbusSlave232::crc(unsigned char*, unsigned char, unsigned char)
- >> ModbusSlave232::preset_multiple_registers(unsigned, unsigned char, unsigned char*, int*)
- >> ModbusSlave232::read_holding_registers(unsigned, unsigned char, int*)

[Called By]

- >> update_modbus()

ModbusSlave232::configure(unsigned char, long, char) (Thumb, 76 bytes, Stack size 8 bytes, modbusslave232.o(i._ZN14ModbusSlave2329configureEhlc))

[Stack]

- Max Depth = 272 + Unknown Stack Size
- Call Chain = ModbusSlave232::configure(unsigned char, long, char) ⇒ mbed::SerialBase::baud(int) ⇒ serial_baud ⇒ error ⇒ exit ⇒ fflush ⇒ _do_fflush ⇒ _fflush ⇒ _writebuf ⇒ _sys_write ⇒ serial_init ⇒ mbed_assert_internal (Cycle)

[Calls]

- >> mbed::SerialBase::format(int, mbed::SerialBase::Parity, int)
- >> mbed::SerialBase::baud(int)

[Called By]

- >> $Super$$main

AjK::MODSERIAL_callback::MODSERIAL_callback() (Thumb, 18 bytes, Stack size 0 bytes, modserial.o(i._ZN3AjK18MODSERIAL_callbackC1Ev))
[Address Reference Count : 1]

- modserial.o(i._ZN3AjK9MODSERIALC1E7PinNameS1_PKc)

AjK::MODSERIAL_callback::MODSERIAL_callback__sub_object() (Thumb, 0 bytes, Stack size 0 bytes, modserial.o(i._ZN3AjK18MODSERIAL_callbackC1Ev), UNUSED)

AjK::MODSERIAL::initDevice() (Thumb, 2 bytes, Stack size 0 bytes, modserial_nucleo_f401re.o(i._ZN3AjK9MODSERIAL10initDeviceEv))

[Called By]

- >> AjK::MODSERIAL::init(int, int, PinName)

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

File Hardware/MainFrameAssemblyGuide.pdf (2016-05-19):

Parts:

PVC base board
PVC motherboard wall
6 x 2” diameter PVC standoffs
6 x 2” self adhesive antiskid surface pads Punched angle
2 x 31 ½”
4 x 30”
4 x 24”
7 x 18”
4 x 6”
2 x 1”
26 x ⅜”-16 1” bolts
46 x ⅜”-16 ½” bolts
83 x ⅜”-16 nuts
84 x ⅜” washers
10’ weatherstrip tape

Tools:

⅜” ratchet
⅜” crescent wrench

Instructions:

1. Place the PVC base board on a flat surface with the faux wood side down. The 6 holes on the left side outline the base of the electronics chamber, and the 10 holes on the right side outline the base of the grow chamber.

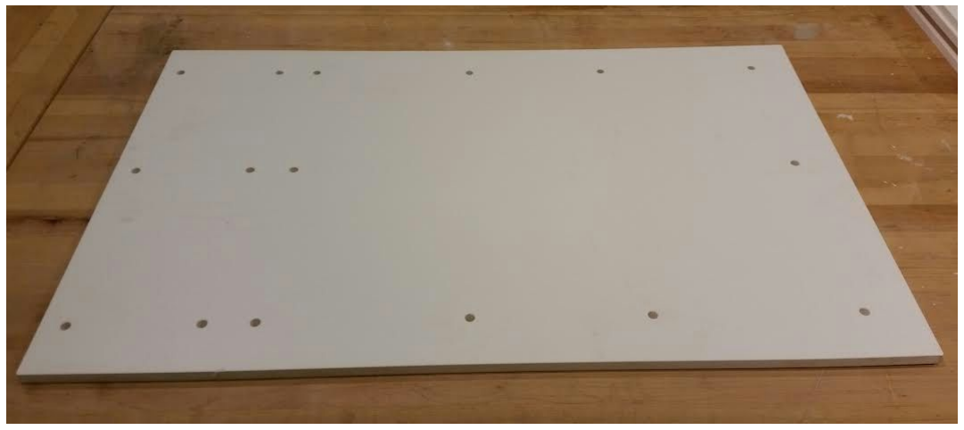
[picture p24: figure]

2. Lay out 2 of the 6” punched angle lengths electronics side and 2 of the 24” punched angle lengths on the grow side as shown.

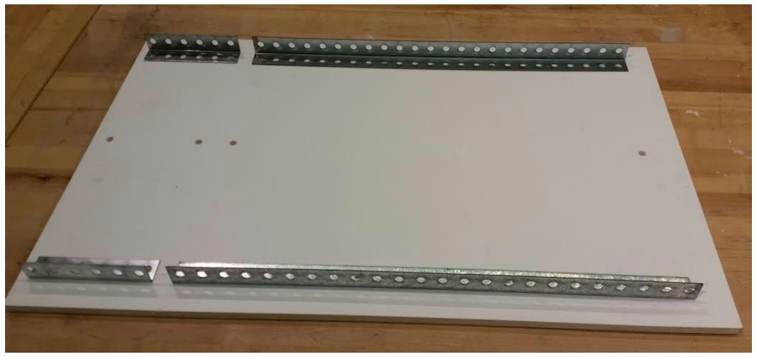
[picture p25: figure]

3. Lay out 2 of the 18” punched angle lengths on the outermost sides of the base board and another on the right side of the electronics chamber side as shown. Secure this base frame with the 1” bolts on all noncorner through holes. Use washers on both sides of the board and put the heads of the bolts on the underside of the board.

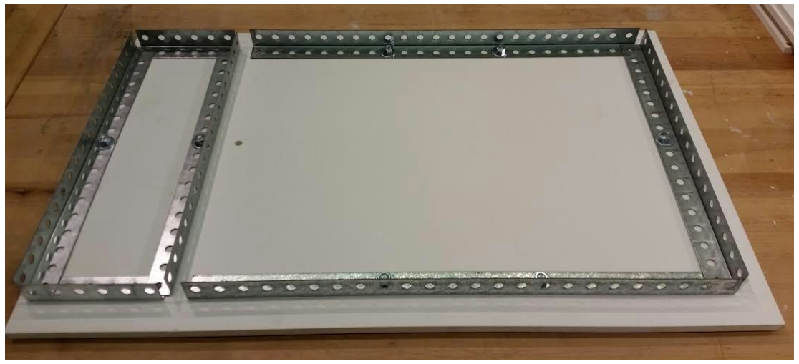
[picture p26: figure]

4. Place 1” bolts through 4 of the standoffs making sure the heads of the bolts are on the countersunk side of the standoffs.

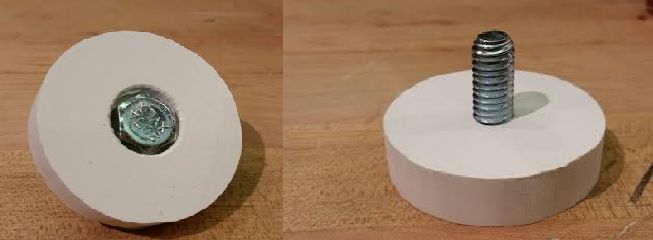
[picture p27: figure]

5. Insert these standoffs through the 4 outermost corner holes of the base board with the standoffs on the underside of the base board. Do not use washers on either side of the bolt. Make sure the bottom of your base board matches the picture below.

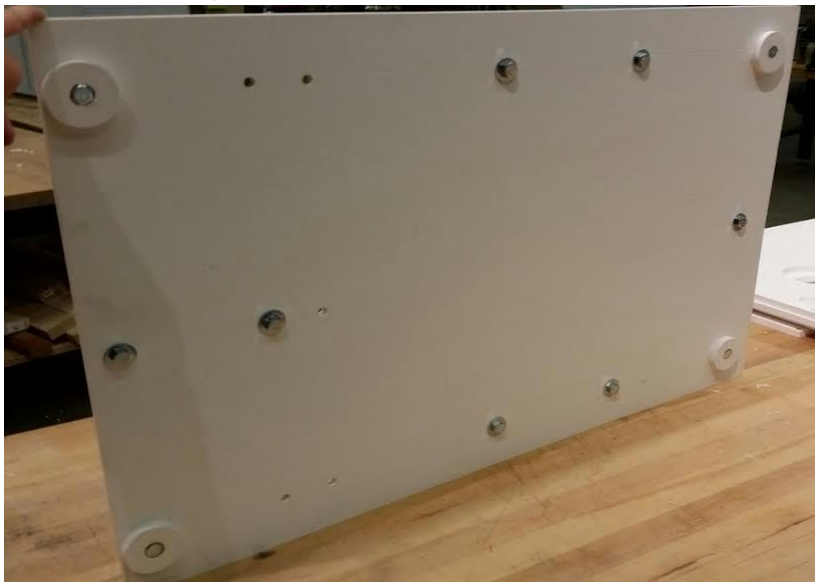
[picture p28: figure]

6. Set the PVC motherboard wall on the table with the faux wood side down. Place 2 of the 30” punched angle lengths along the length of the board. Use 1” bolts with washers on each side to secure the 30” lengths to the board through the 4 aligning noncorner through holes. Orient the bolts such that heads are on the punched angle side of the wall.

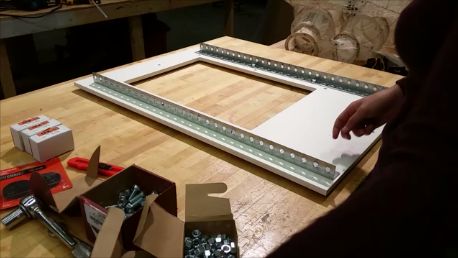
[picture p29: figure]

7. Place 1 of the 18” punched angle lengths along the top of the motherboard wall and use a 1” bolt to secure the 18” length at its center through the PVC motherboard wall.

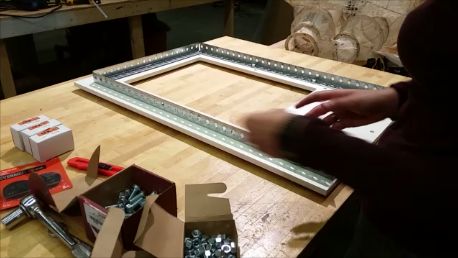
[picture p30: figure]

8. Now align the motherboard wall perpendicular to the base board, with the punched angle parts secured to the motherboard wall facing the grow chamber side as shown. Place 1 more of the 18” punched angle lengths at the base of the motherboard wall on the grow chamber side. Secure the 18” length to the motherboard wall and 18” length on the other side using 1” bolts with no washers at the two bottom corners and single center through hole. Orient the bolts such that heads are on the grow side of the motherboard wall.

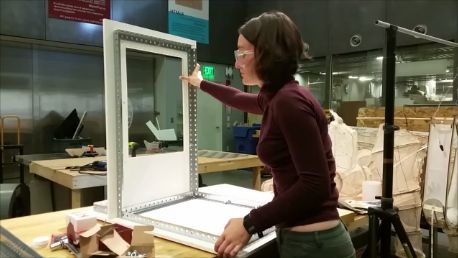
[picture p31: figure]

9. Set the frame on its side to insert the last standoffs and 1” bolts through the base board such that the bottom looks as shown. For the last 2 standoffs, do not use washers. For the rest, use washers only on the bottom of the base board. Tighten all bolts and standoffs with the ratchet and crescent wrench.

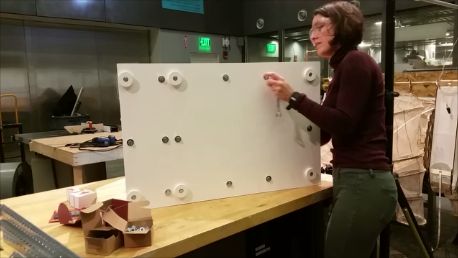
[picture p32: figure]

10. Peel the paper off the backs of the 6 antiskid pads and stick them to the standoffs as shown.

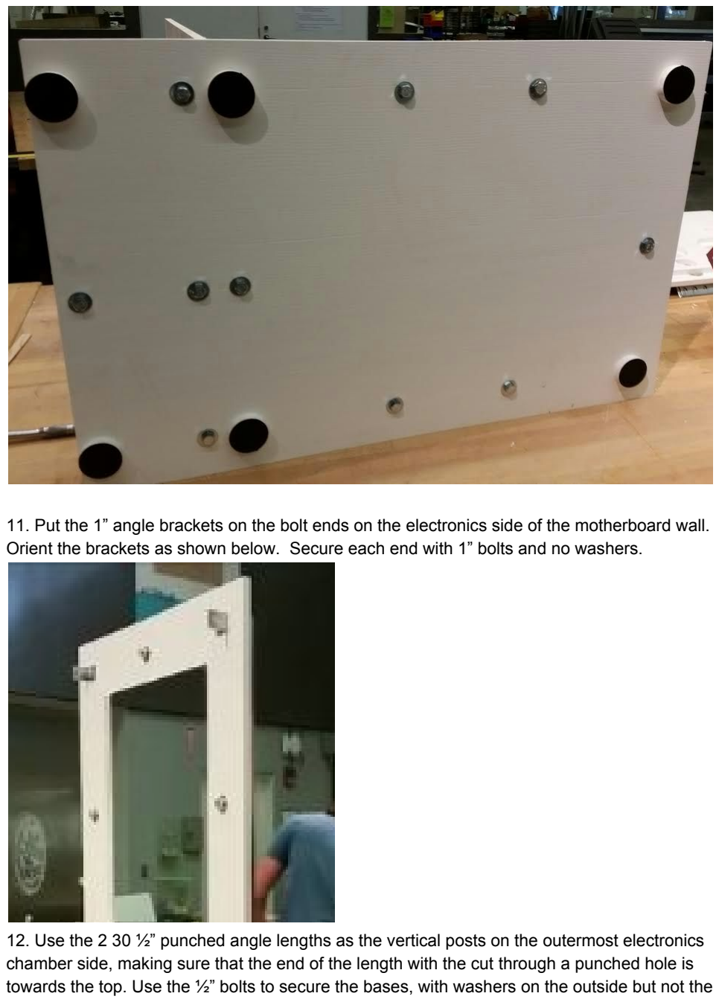
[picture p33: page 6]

11. Put the 1” angle brackets on the bolt ends on the electronics side of the motherboard wall. Orient the brackets as shown below. Secure each end with 1” bolts and no washers.
12. Use the 2 30 ½” punched angle lengths as the vertical posts on the outermost electronics chamber side, making sure that the end of the length with the cut through a punched hole is towards the top. Use the ½” bolts to secure the bases, with washers on the outside but not the inside of the punched angle corners. Make sure the intersections between angle parts are approximately perpendicular.

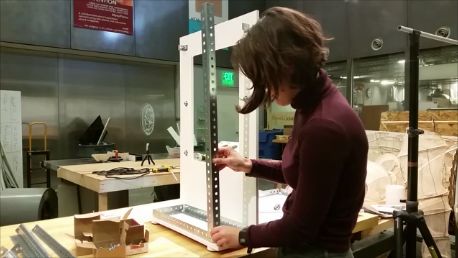
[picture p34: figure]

13. Use the last 2 30” punched angle lengths for the outermost vertical posts on the grow chamber side of the frame. Again, use ½” bolts with washers on the outside and not the inside of the punched angle corners. Make sure the intersections between angle parts are approximately perpendicular.

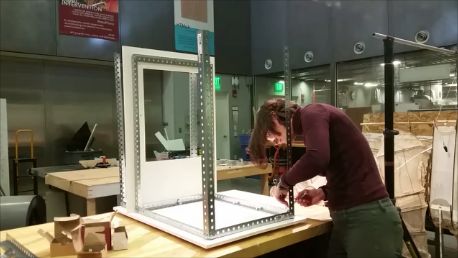
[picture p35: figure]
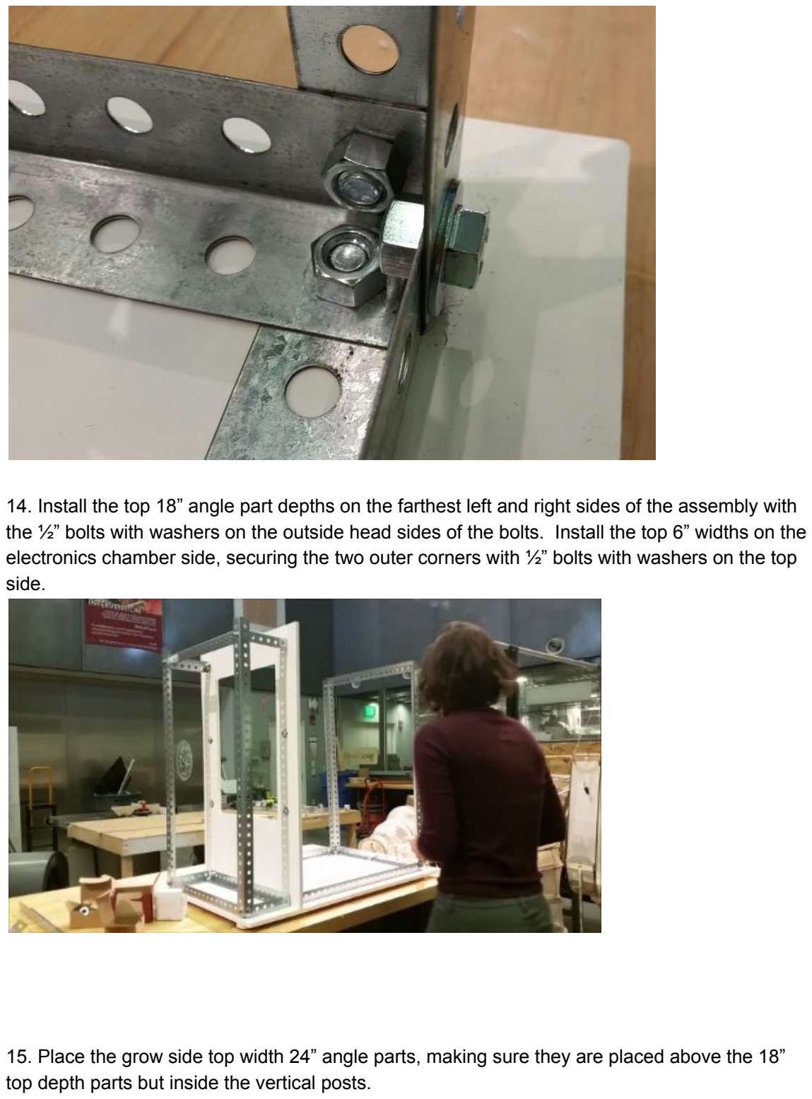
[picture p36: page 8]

14. Install the top 18” angle part depths on the farthest left and right sides of the assembly with the ½” bolts with washers on the outside head sides of the bolts. Install the top 6” widths on the electronics chamber side, securing the two outer corners with ½” bolts with washers on the top side.
15. Place the grow side top width 24” angle parts, making sure they are placed above the 18” top depth parts but inside the vertical posts.

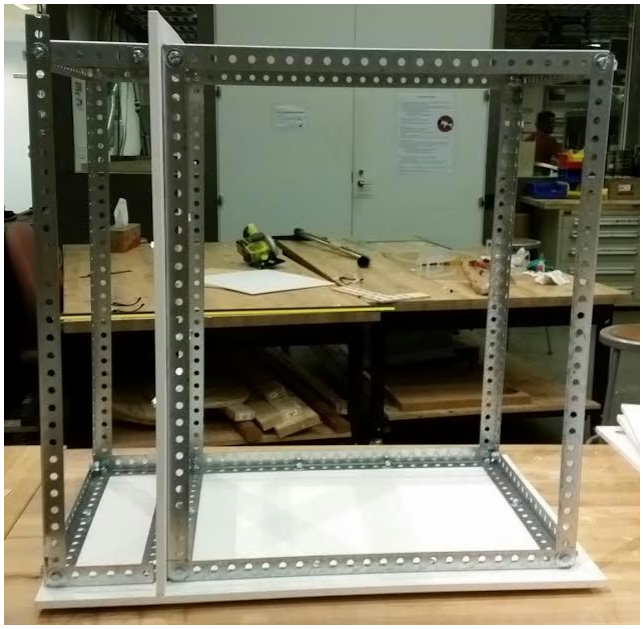
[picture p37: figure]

16. Get a topdown view of the assembly now, by either standing on the table or bringing the assembly down onto the floor. Secure the 6 corners with the last ½” bolts, with heads and washers on the top of the frame and nuts without washers on the underside.
17. Do some last adjusting if the frame is crooked. Check each corner to make sure all pairs of angle bracket are perpendicular to each other. You may have to do some loosening and retightening of bolts.
18. Now to make the seal between the main frame and jacket. Take your weatherstripping and line the base of the PVC base board on the grow side with it. Make sure the edge of the weatherstripping is right along the edge of the base but not protruding over the edge as this will make sliding the clam shell jacket over difficult or impossible. Do the same along the edge of the grow side of the PVC motherboard wall.

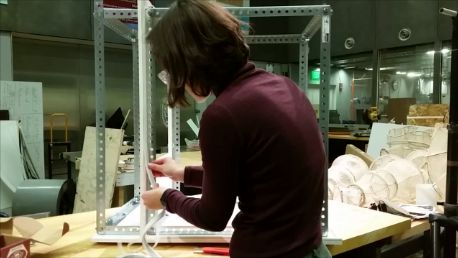
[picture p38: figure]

19. Now, weatherstrip around the edge of the PVC motherboard wall cutout on the electronics chamber side. This will act as the seal when the electronics panel is pressed against the weatherstripping and bolted onto the motherboard wall.

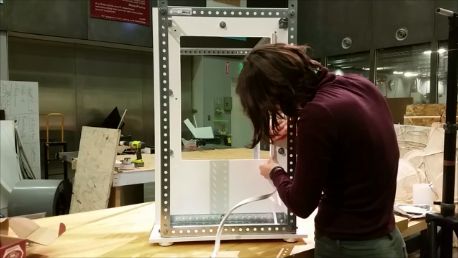
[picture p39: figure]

20. Take the laser cut front upper plate and back plate and install onto front and back faces of the punched angle frame on the electronics side, respectively. Use the ½” bolts and washers on the outer face and just nuts on the inner face.

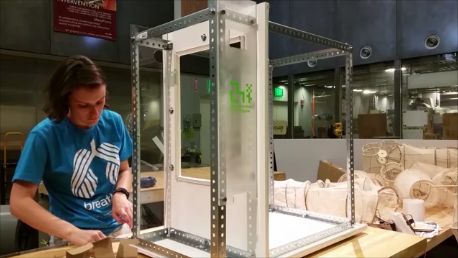
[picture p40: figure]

21. Find 20 of the magnets and put VHB tape onto one side, making sure the polarity orientation is the same for all 20. Tape 4 of the magnets along the punched angle that outlines the place of the front lower plate and 6 of the magnets along the punched angle that outlines the place of the side plate.
22. Put the front lower plate against the punched angle, and align another set of magnets with those taped directly to the punched angle. Tape the new magnets onto the front lower plate.

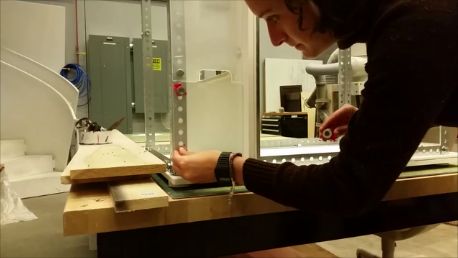
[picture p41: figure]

23. Do the same with the last 6 magnets and the side plate.

Assemble the kit section.

This is the “wet lab” section that sits underneath the electronics motherboard. It contains the materials for water chemistry balancing and managing a yeast reactor and also includes some safety equipment.

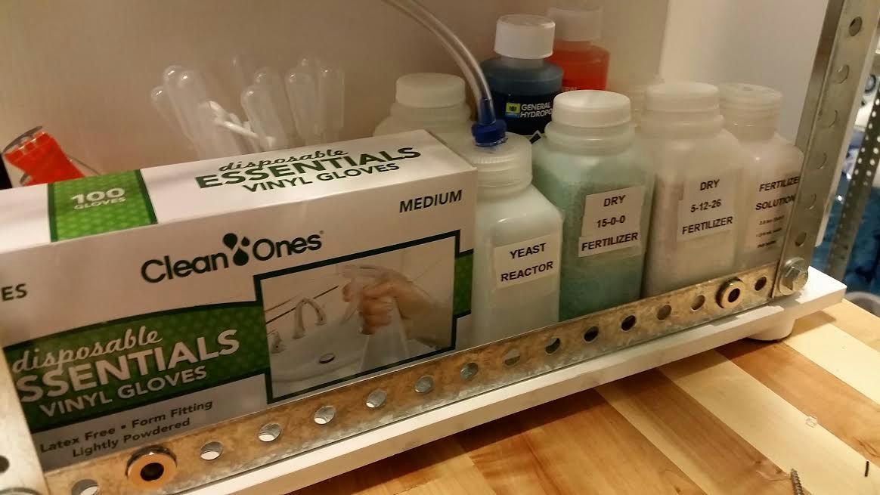
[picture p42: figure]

Yeast reactor: Drill a ⅜” hole in the lid of the bioreactor bottle. Hot glue the oneway valve into the opening, making sure that the arrow on the valve is pointing upwards, out of the bottle. Cut 2’ of the ⅜” tubing and push one end onto the oneway valve and route the other through the bottom left hole in the electronics panel through to the grow chamber side. The bottle behind the yeast reactor is filled with sugar.

To the right of the yeast reactor bottle are the four fertilizer bottles. Two contain dry fertilizer while the other two contain solutions of the fertilizers in water. Behind those fertilizer bottles sits the pH balancing kit.

Not seen behind the box of gloves are extra packets of yeast, measuring spoons, safety glasses, and pipettes.

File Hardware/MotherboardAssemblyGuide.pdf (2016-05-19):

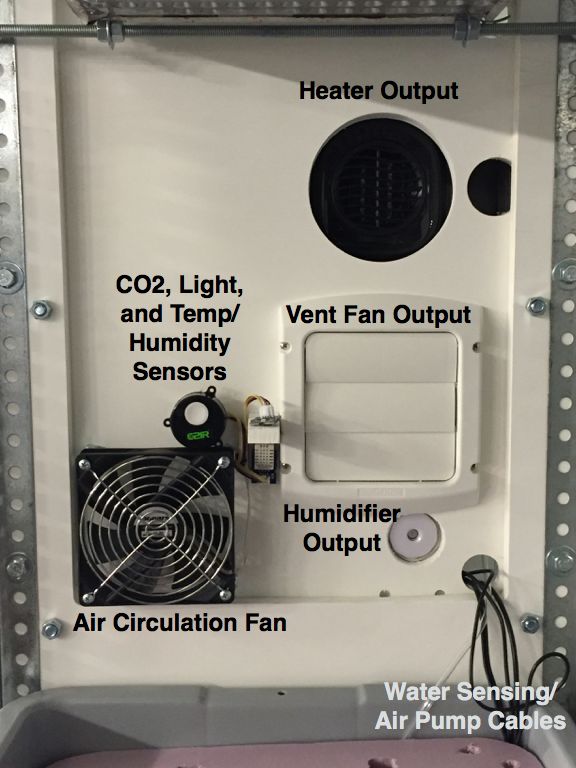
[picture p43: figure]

Plant side of electronics panel

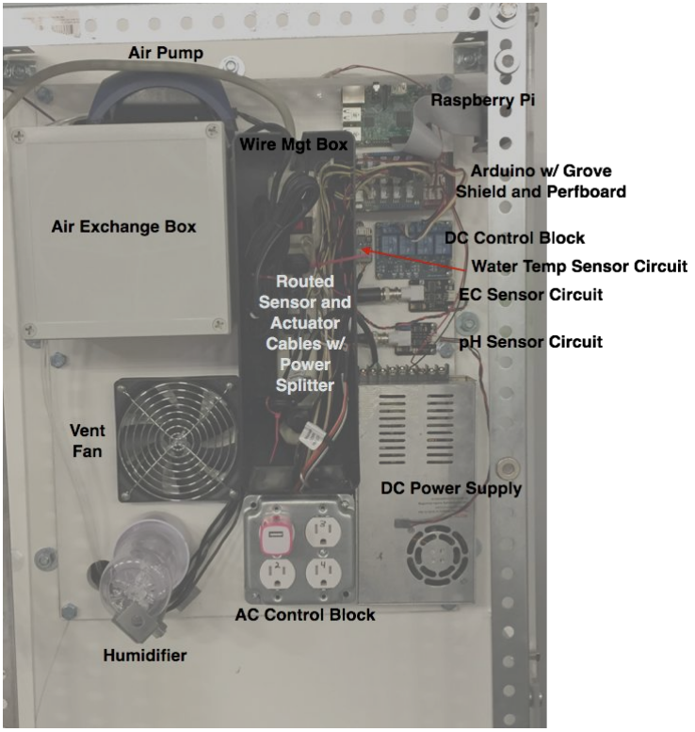
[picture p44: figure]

User side of electronics panel

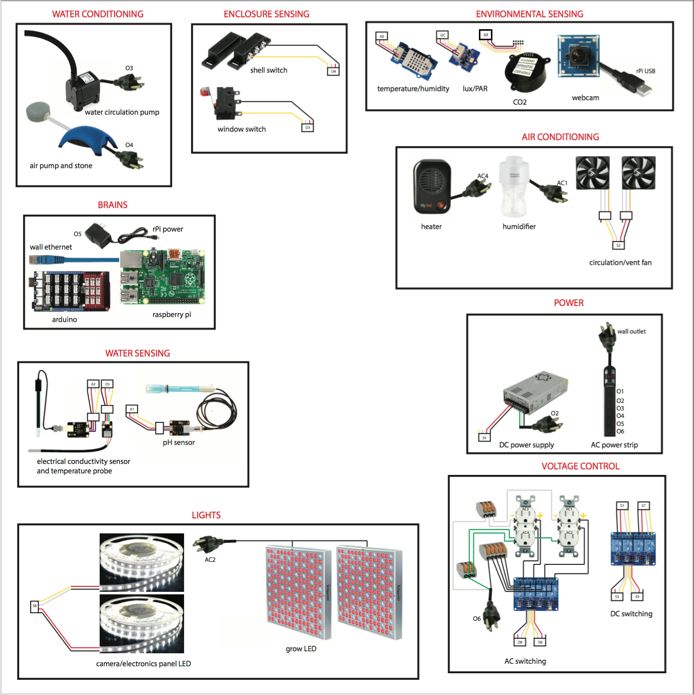
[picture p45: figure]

(a larger zoomable copy of this schematic is in the documentation)

*Assembling the electronics panel is tricky but manageable, you just have to consult two or three of the diagrams at once. The pictures of position give an indication of where the components are placed on the panel. The schematic gives real wiring/polarity directions for assembling the subcomponents. Soldering will be required to join some wires.

1. 120VAC Control Module
a. Materials

i. 2-gang box bottom
ii. | 2-gang box top
iii. | 2-channel AC socket x2
iv. | 4-channel relay
v. Female jumpertogrove cable x2
vi. | 6-channel, maletofemale jumper wire
vii. | 6 foot, 3-prong extension cable
viii. | 3-port, Wago, lever connector x2
ix. | 5-port, Wago, lever connector
x. 0.5” screw x4
b. Tools
i. Medium, phillips screwdriver
ii. | Wire strippers
iii. | Hot glue gun
iv. | Hammer
c. Tools Consumables
i. Hot glue
ii. | Electrical Tape
iii. | Duct tape
iv. | Permanent Marker
d. Instructions
i. Create shortened AC connector (10” total length, male).
1. Cut the extension cord 8” away from the base of the male side of
| the cable. The total cable length will be approximately 10”.
2. Strip off approximately 2” of the outer encasement from the cable.
3. Strip off approximately ½” of insulation from each of the three
| wires that are now exposed.
ii. | Tap out a center tab from the 2-gang box bottom
iii. | Feed the exposed wire end on the extension cable through this hole and
| connect to the wago lever connectors. IMPORTANT:you must put the
| extension cable through the hole beforeattaching the connectors
| otherwise the cable will not fit through later in the assembly.
1. Connect the black wire (hot) to a 5-port connector
2. Connect the white wire (neutral) to a 3-port connector
3. Connect the green wire (ground) to a separate 3-port connector iv. Create intermediary AC wires (6” segments x6 BLK, x3 GRN, x3 WHT)
1. Using the remains of the extension cable cut x6 6” segments and
| pull out all the wires from the encasement.
2. Strip each wire such that there is approximately 1” of exposed wire
| on one end and ½” of exposed wire on the other end. Create x6
| black wires, x3 green wires, and x3 white wires.
v. Create x2 modified AC sockets

1. Break off the tab connecting the “hot” screw terminals.The “hot” screw terminals have gold screws and are labeled “hot” on the back of the sockets. Note: this tab is located in between the screw terminals and is a very small lip that is the same gold color as the plating around it.
2. Using the permanent marker, label the top plug on one of the sockets “1” and the bottom plug “2”. Do the same on the other socket, however, label them “3” and “4”.
3. Bend the protruding mounting tabs that are located on the top and bottom of the socket so they form 90 degree angles and are able to fit into the 2-gang box
4. Connect the 1” end of a black wires to each “hot” screw terminal on the socket. Remember: the “hot” terminals have the golden screws and are labeled on the backside of the socket. You will connect two black wires per socket.
5. Connect the 1” end of a white wire to either of the neutral screw terminals on the socket. These terminals have silver screws and are also labeled on the back of the socket.
6. Connect the 1” end of a green wire to the ground screw terminal on the socket. The ground screw terminal is green.
vi. | Connect the ground and common from both AC sockets to the Wago
| 3-port lever connectors containing the ground and common from the
| extension cable, respectively.
vii. | Connect the AC sockets to the relay block.
1. Connect the black wire (“hot”) from the socket labeled “1” to the
| middle screw terminal labeled K1 on the relay block. Do this for
| sockets 2,3,4 connecting to K2, K3, and K4 respectively.
2. When viewing the screw terminals on the relay block head on,
| connect x4 black wires to the left terminal in each of K# block.
3. Connect all 4 of the black wires connected to the left terminal on
| the relay block to the Wago 5-port lever connector containing the
| black wire from the extension cable.
viii. | Screw the sockets to the 2-gang box top such that the 1-2 socket is on
| the left and the 3-4 socket is on the right.
ix. | Connect control cables to the relay block
1. Connect the 6-channel, maletofemale jumper cables to the 6
| exposed header pins on the relay block
2. To keep headers securely fastened, squirt a hefty amount of hot
| glue around the connection.
3. Using a single female jumpertogrove cable, connect the black
| wire on the grove cable to the wire attached to GND on the
| relay,the whitewire on the grove cable to the wire attached to IN1
| on the relay, the yellowwire on the grove cable to the wire

attached to IN2 on the relay. This cable will connect to the D8 receptacle on the arduino grove shield so it is recommended you use the permanent marker to label the end of the connector “D8”.
4. Using the other female jumpertogrove cable, connect the red wire on the grove cable to the wire attached to VCC on the relay,the whitewire on the grove cable to the wire attached to IN3 on the relay, the yellowwire on the grove cable to the wire attached to IN4 on the relay. This cable will connect to the D6 receptacle on the arduino grove shield so it is recommended you use the permanent marker to label the end of the connector “D6”.
5. For each cable, hot glue the connection between the maletofemale jumper cable and the female jumpertogrove cable and then wrap the connection in electrical tape once the hot glue dries
6. Route these cables out of the box from the same hole that was knocked out to insert the extension cable.
x. Insulate the bottom of the relay block
1. Place a layer of electrical tape on the bottom of the relay block
2. Place a layer of duct tape over the layer of electrical tape on the bottom of the relay block
xi. | Using the small screws, attach this module to the motherboard on top of
| the footprint labeled “AC”
xii. | Screw in the top of the 2-gang box
xiii. | Once the wire management module is built, the extension cable will plug
| into the power strip.
xiv. | Test the device by plugging in something to each AC port. Use 5V and
| the ground pin of an Arduino to power and activate each relay channel on
| the relay block.
2. 12V-30A Power Supply Module
a. Materials
i. 12V-30A power supply
ii. | 6 foot, 3-prong extension cable
iii. | 4-pin, buckled, 50cm grove cable
iv. | 14” x 1” mounting tape
b. Tools
i. Medium, phillips screwdriver
ii. | Wire strippers
iii. | Tape measure
iv. | Multimeter
c. Instructions
i. Create shortened AC connector (10” total length, male).

1. Cut the extension cord 8” away from the base of the male side of the cable. The total cable length will be approximately 10”.
2. Strip off approximately 2” of the outer encasement from the cable.
3. Strip off approximately 1” of insulation from each of the three wires that are now exposed.
ii. | Connect shortened AC connector to power supply (BLK-L, WHT-N,
| GRN-GND)
1. Connect the black wire (hot) from the shortened ac connector to
| the screw terminal on the power supply with the “L”symbol
| overhead. Note: a better connection is made by placing the wires
| on the left hand side of the screw so that when the screw is
| tightened (turned to the right), the wire stays within the receptacle.
2. Connect the white wire (neutral) from the shortened ac connector
| to the screw terminal on the power supply with the “N”symbol
| overhead.
3. Connect the green wire (ground) from the shortened ac connector
| to the screw terminal on the power supply with the “GND”symbol
| overhead. Note: the GND, or ground, symbol is the the symbol
| with multiple horizontal lines.
iii. | Create modified grove cable
1. Cut off one side of the grove cable very close to the base. Either
| side will work.
2. Strip off approximately 1” of insulation from the red and black
| wires. Do nothing with the white and yellow wires.
iv. | Connect modified grove cable to the power supply
1. Connect the blackwire from the grove cable to one of the -V
| screw terminals on the power supply.
2. Connect the redwire from the grove cable to one of the +Vscrew
| terminals on the power supply.
v. Tune power supply so it outputs exactly 12V
1. Use the multimeter to probe the +V and -V terminals on the power
| supply. Using the adjustment screw, tune the output voltage to be
| as close to 12V as possible.
vi. | Apply 2 strips of approximately 7” strips of mounting tape to the underside
| of the power supply and place it nearly flush against the AC control
| module. The bottom of the power supply should be tangent with the
| bottom of the AC relay box leaving approximately ¼” gap between the two
| verticals.
vii. | Once the wire management module is built, the AC extension cablewill
| plug into the power strip.
viii. | Once the arduino protoshield module is built, the grove connectorwill
| plug into S4.

### 3. Air Exchanger Module

a. Materials
i. Heater
ii. | 7” x 7” x 5” project box
iii. | USB-to-AC converter
iv. | 6” Fans x2
v. 6” Fan Guards x3
vi. | 4” Louvre
vii. | Humidifier
viii. | 6” x ½” weather stripping
ix. | Air pump
x. Air stone
xi. | 24” of .125” inner diameter tubing
xii. | Small (.5”) screws x4
xiii. | Medium (1”) screws x4
xiv. | Long screws (1.5”) x4
xv. | Standoffs (can just use bolts from frame) x4
b. Tools
i. Power Drill
ii. | 1 ¾” hole saw drill bit
iii. | 4 ½” hole saw drill bit
iv. | 12” x 1” mounting tape
v. Hand file
c. Instructions
i. Create modified project box.
1. A few tips before starting. First mark all holes on the box. Check
| they are in the correct positions. When drilling each hole, drill pilot
| holes first. Then, create groove by running hole saw bit in reverse
| direction. Finish cut by running hole saw bit in forward direction.
| For the large hole saw bit you may need to do the entire cut by
| running the bit in the reverse direction. After cuts are made, clean
| up edges with a file.
2. When viewed from the back of the box, drill a 4 ½” diameter hole
| that is centered 2 ⅜” right and 2 ⅜” up from the bottom left corner.
3. When viewed from the back of the box, drill a 1 ¾” diameter hole
| that is centered 1” left and 2 ⅜” up from the bottom right corner.
4. When viewed from the right of the box (from the front of the box),
| drill a 1 ¾” diameter hole that is centered 1 ½” left and 1 ½” down
| from the top right corner of the box.
ii. | Mount heater into modified project box
1. When looking into the project box with the big hole on the right
| and the little hole on the left the heater will be mounted upside
| down with the front of the heater oriented through the big hole.

The heater will be pushed all the way into the bottom right corner of the box.
2. Make sure the heater is switched ON. Route the heater able through the right side hole then apply mounting tape to the all sides of the heater that will be in contact with the project box. iii. Attach project box to the motherboard
1. Place the modified project box with the heater inside of it onto the
| motherboard on the section labeled “air XC”.
2. Secure the box by screwing x4 small screws into the corners. Seal
| the project box cover. Drop the screws into the holes and use a
| screwdriver to drive them into the PVC.
iv. | Assemble and mount the air pump on top of the air exchange box
1. Push one end of the tubing onto the end of the air pump. Route
| this line down the left side of the motherboard and pop the tube
| through the hole on the lower left side of the panel.
2. The power cord from the air pump will go into the wire
| management module and plug in directly to the power stip. The air
| pump will therefore always be running when the power is on.
3. Hot glue the feet of the pump so that the pump does not fall off the
| air exchange box when the motherboard panel is jostled. Mount
| the air pump as far from the wall as possible because wires will
| have to be able to make it through that hole.
v. Assemble and mount the vent fan
1. Place one of the fans on top of the lower large hole of the
| motherboard panel such that the air is blowing into the grow
| chamber. There is a graphic on a side of the fan with arrows that
| indicate which direction the fan blows air as well as which direction
| the fan spins.
2. Place a fan guard over top of the fan such that it is on the surface
| furthest from the inside of the grow chamber.
3. Using x4 of the medium sized screws, mount the fan to the
| motherboard.
vi. | Assemble and mount the louvre
1. The inner cylinder on the louvre protrudes too far into the opening
| of the motherboard. Shorten the cylinder with an exacto knife by at
| least half its length.
2. The louvre will be mounted on the inside of the motherboard, on
| the surface inside the grow chamber. Make sure the louvre is
| oriented such that gravity keeps them closed.
3. Using x4 of the small sized screws, mount the louvre to the
| motherboard.
vii. | Assemble and mount the circulation fan

1. Mount the circulation fan on the inside of the electronics panel in the lowest possible position that is closest to the front of the bot. Make sure the fan is oriented such that it is blowing into the chamber. In order to generate airflow, standoffs (3 washers) must be placed in between the fan and the motherboard. Also for safety, place a fan guard on the surface furthest into the grow chamber. Use the long screws to attach to the motherboard. For clarity, the order of materials is: inside of motherboard, standoffs, fan, fan guard, long screws running through to hold it all together.
2. The circulation and vent fan will be wired together. Consult the schematic for polarity. Each fan has a three channel cable. The gold cable is ground, and the center cable is power (12V). The third cable is not used. Taking a grove cable, connect red and black to the circulation fan power and ground, and white and yellow to the power and ground of the vent fan. The connector end of the grove cable will then plug into S2.
viii. Assemble and mount the humidifier
1. The humidifier mount bracket is created from a 6” long section of
| stamped angle. First, a notch is cut down the spine of the angle
| about 1” in length with a bandsaw. Next, using a metal brake,
| each side of the angle is flared out at the 1” mark to create a tab
| perpendicular to the main length of slotted angle. Finally, bolt a 1”
| section of stamped angle to the end of the bracket to prevent the
| humidifier from slipping out.

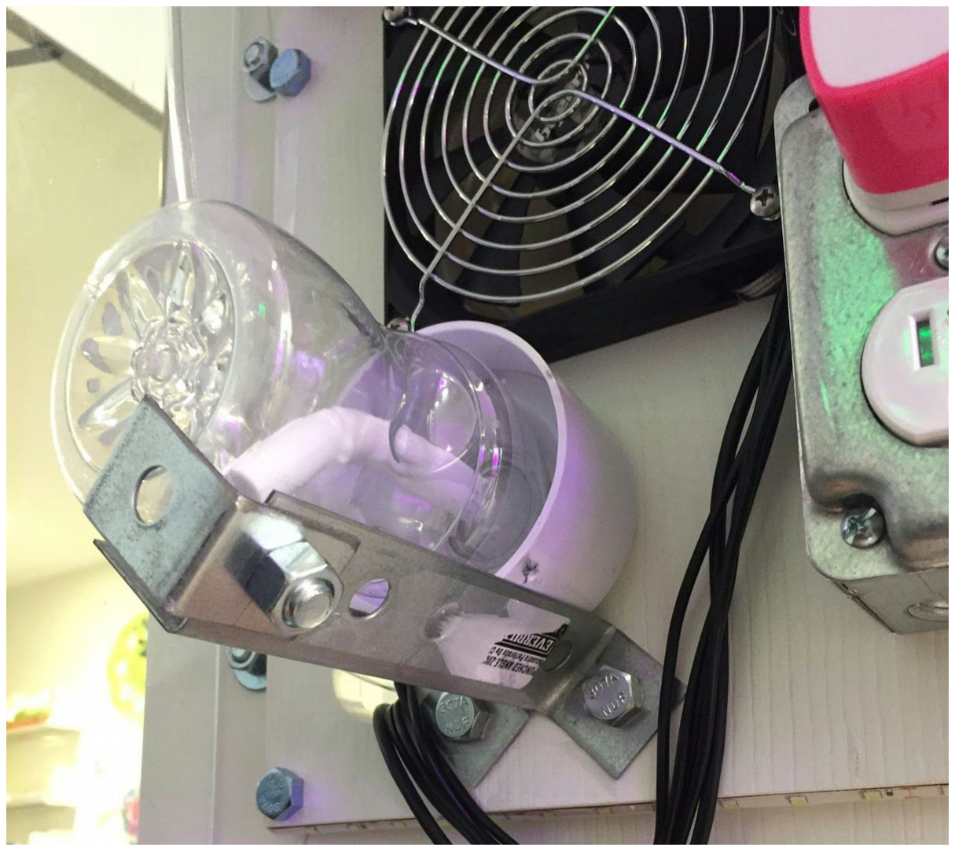
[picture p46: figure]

2. Drill holes for humidifier, diameter 1 ¾” 4” from right side and 2 3/4” from bottom (when looking at grow chamber side). Drill two 5/16” humidifier mount holes 1 ¾” apart and 2” below the center of the humidifier hole. The bracket will help with alignment. Using a ⅜-16 tap, thread the 5/16” holes.
3. Bolt in the humidifier mount to the board.

4. Apply weather stripping to the lower top surface of the humidifier. The part that will sit against the motherboard. NOT the part that will protrude through it.
5. When the humidifier is pressed up against the motherboard, make sure that the usb port is facing directly to the right. With the usb port facing to the right, carefully take off the plastic encasement of the wick. Note how this encasement fits back onto the humidifier. Using a heat source, either a heat gun, lighter, or something equivalent, slowly head the center of the encasement and slowly bend the piece down. The entire purpose of doing this is so that the wick can suck up water when the humidifier is placed in a horizontal position so make sure the way you bent the wick complies with this goal as well as orienting the usb port to the right.
6. Press fit the modified humidifier into the mount and connect the usb port. Route the cable through the wire management unit and plug it into the USB-to-AC converter. Plug in the converter to the AC Control module in port 2.

### 4. Wire Management Module

a. Materials
i. Wire management box
ii. | 6-channel power strip
iii. | 34” x 1” mounting tape
b. Tools
i. Power drill
ii. | .5” diameter drill bit
iii. | 1.5” hole saw bit
c. Instructions
i. Viewed from the right side of the wire management box, drill a 1/2”
| diameter hole centered 1” down and ¼” to the left from the upper right
| corner of the box and such that the bottom of the hole is flush with the
| motherboard. This hole will accommodate the USB port on the arduino,
| so you gauge position necessary by the height the arduino sits above the
| motherboard.
ii. | Viewed from the right side of the wire management box, drill a 1.5”
| diameter hole centered 1 1/2” down and 2” to the left from the upper right
| corner of the box.
iii. | Viewed from the right side of the wire management box, drill a 1.5”
| diameter hole centered 6” down and 1/2” left of the upper right corner of
| the box and such that the bottom of the hole is flush with the
| motherboard.

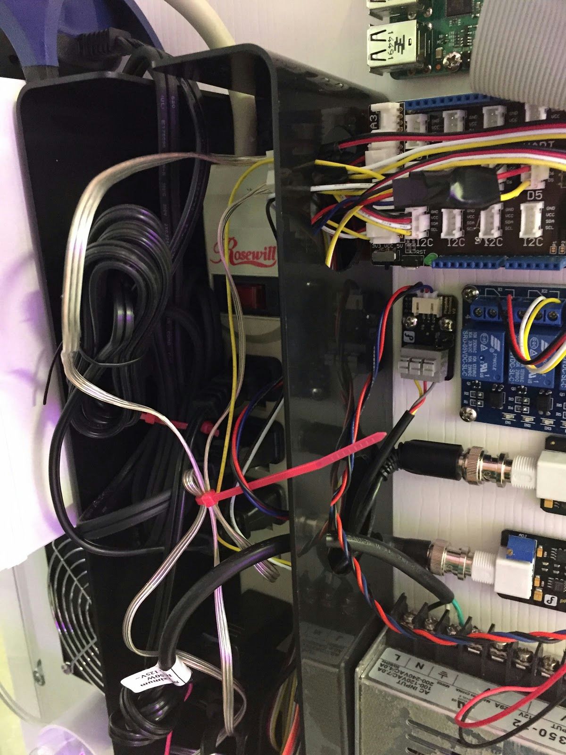
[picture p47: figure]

The two holes will provide cable paths to the Arduino and for the water sensors

iv. | Viewed from the top of the wire management box, using a 10” strip of
| mounting tape to secure the power strip to the lower left corner of the
| inside of the box such that the trailing power cable will protrude towards
| the top of the motherboard.
v. Using 2 strips of 12” segments of mounting tape, attach the top of the wire
| management module flush with the top of the air exchange box and
| 12V-30A power supply. There should be approximately 1” gap between
| the top of the AC control module and the bottom of the wire management
| module.

### 5. DC Control Module

a. Materials
i. 4-channel relay block
ii. | Female jumpertogrove cable x2
iii. | 4-pin, buckled, 10cm grove cable
iv. | 6-channel, maletofemale jumper wire
v. small .5” screws x4
b. Tools
i. Wire strippers
ii. Hot glue gun
c. Tools Consumables
i. Hot Glue
ii. Electrical Tape

iii. Permanent Marker
d. Instructions
i. Connect control cables to the relay block
1. Connect the 6-channel, maletofemale jumper cables to the 6
| exposed header pins on the relay block
2. To keep headers securely fastened, squirt a hefty amount of hot
| glue around the connection.
3. Using a single female jumpertogrove cable, connect the black
| wire on the grove cable to the wire attached to GND on the
| relay,the whitewire on the grove cable to the wire attached to IN1
| on the relay, the yellowwire on the grove cable to the wire
| attached to IN2 on the relay. This cable will connect to the S3
| receptacle on the arduino protoboard module so it is
| recommended you use the permanent marker to label the end of
| the connector “S3”.
4. Using the other female jumpertogrove cable, connect the red
| wire on the grove cable to the wire attached to VCC on the
| relay,the whitewire on the grove cable to the wire attached to IN3
| on the relay, the yellowwire on the grove cable to the wire
| attached to IN4 on the relay. This cable will connect to the S9
| receptacle on the arduino protoboard module so it is
| recommended you use the permanent marker to label the end of
| the connector “S9”.
5. For each cable, hot glue the connection between the
| maletofemale jumper cable and the female jumpertogrove
| cable and then wrap the connection in electrical tape once the hot
| glue dries.
ii. | Connect the switch cables to the relay block
1. Cut the 10cm grove cable into 2 segments. One segment ⅔ of the
| cable and the other ⅓.
2. Strip approximately ½” of insulation off the tips of each cable
3. On the longer cable, connect blackto the center port of the K1
| screw terminal (K1-SW). Connect redto the left port of the K1
| screw terminal (K1-ON). Left is defined by viewing the screw
| terminals from the front, or looking into the board. Connect white
| to the center port of the K2screw terminal (K2-SW).Connect
| yellowto the left port of the K2screw terminal (K2-ON). Left is
| defined by viewing the screw terminals from the front, or looking
| into the board. This cable will connect to the S1receptacle on the
| arduino protoboard module so it is recommended you use the
| permanent marker to label the end of the connector “S1”.
4. On the shorter cable, connect blackto the center port of the K3
| screw terminal (K3-SW). Connect redto the left port of the K3

screw terminal (K3-ON). Left is defined by viewing the screw terminals from the front, or looking into the board. Connect white to the center port of the K4screw terminal (K4-SW).Connect yellowto the left port of the K4screw terminal (K4-ON). Left is defined by viewing the screw terminals from the front, or looking into the board. This cable will connect to the S7receptacle on the arduino protoboard module so it is recommended you use the permanent marker to label the end of the connector “S7”.
iii. Insulate the bottom of the relay block
1. Place a layer of electrical tape on the bottom of the relay block
2. Place a layer of duct tape over the layer of electrical tape on the
| bottom of the relay block
iv. | Mount the relay block onto the motherboard
1. Using the small screws, mount the relay block to the segment on
| the board labeled “DC”

### 6. Water Sensors Module

a. Materials
i. EC and Water Temperature Sensor
ii. | pH Sensor
iii. | small .5” screws x6
iv. | Male jumpertogrove cable x3
b. Tools
i. Small, phillips screwdriver ii. Hot glue gun
c. Tools Consumables
i. Hot Glue
ii. Electrical Tape
d. Instructions
i. Build the temperature sensor module
1. Plug in the temperature sensor (the silver cylinder with a wire
| coming out of it) to the temperature sensor PCB. The yellowwire
| goes to the Aterminal, redwire to the Bterminal, and greywire to
| the Cterminal.
2. Plug in the small red, black and green cable into the temperature
| sensor PCB. Using a male jumpertogrove cable, connect the red
| grovewire to the red sensorwire, the black grovewire to the
| black sensor wire, and the yellowgrove wire to the green
| sensorwire.
3. This cable will connect to the D5receptacle on the arduino grove
| shield module so it is recommended you use the permanent
| marker to label the end of the connector “D5”.
ii. | Mount the temperature sensor module to the motherboard

1. Using two electronics screws, mount the temperature sensor to the two predrilled holes that sit directly to the left of the DC relay module. The module should be oriented such that the green, red, and black wires are towards the top of the motherboard.
2. Route all cables coming from the PCB through the lower drilled hole in the wire management module. Route the grove cable through the upper drilled hole in the wire management module. Route the sensor through the bottom slat in the wire management module and through the bottom hole leading into the grow chamber. Once the panel is connected to the chamber, snake the sensor into the corner of the water tray such that it is beneath the styrofoam grow tray.
iii. Build the EC sensor module
1. Like the temprature sensor, use two screws to mount the EC
| board directly below the DC relay module. Connect the
| corresponding EC probe and route through the center hole in the
| wire management box and route down and out the bottom hole to
| the grow chamber.
iv. Build the pH sensor module
1. Mount the pH board below the EC board and also connect and
| route the cable through the wire management box and down and
| out through the hole into the grow chamber.

### 7. Water Circulation Module

a. Materials
i. Foam tray with holes cut for the sensors and horticubes
ii. | 12” of .5” inner diameter tubing
iii. | Aquarium water pump
iv. | reservoir tub
b. Tools
i. Scissors
ii. ShopBot
c. Instructions
i. Use the ShopBot to cut the foam tray.
ii. | Place the aquarium pump in the reservoir tub and attach the tube to the
| outlet of the pump
iii. | Place the sensors through the holes in the foam tray so that the ends
| stick in the water. Make sure that the tips are always in liquid, either
| water or the solutions they came with.

### 8. Arduino Mega Protoshield Module

a. Materials
i. Protoshield package

ii. | Grove connector sockets x9
iii. | Wirewrapping wire assortment
b. Tools
i. Wire strippers
ii. | Soldering iron
iii. | Wire wrapping tool
c. Tools consumables
i. Solder
ii. | Solder wick
iii. | Permanent marker
d. Instructions
i. Solder all header pins onto the shield
ii. | Label special grove connector sockets (S1-S9)
iii. | Solder S1-S9 onto the shield as shown below. The receptacle pins are
| slightly smaller than the holes in the perfboard so you will need to bend
| them out slightly.

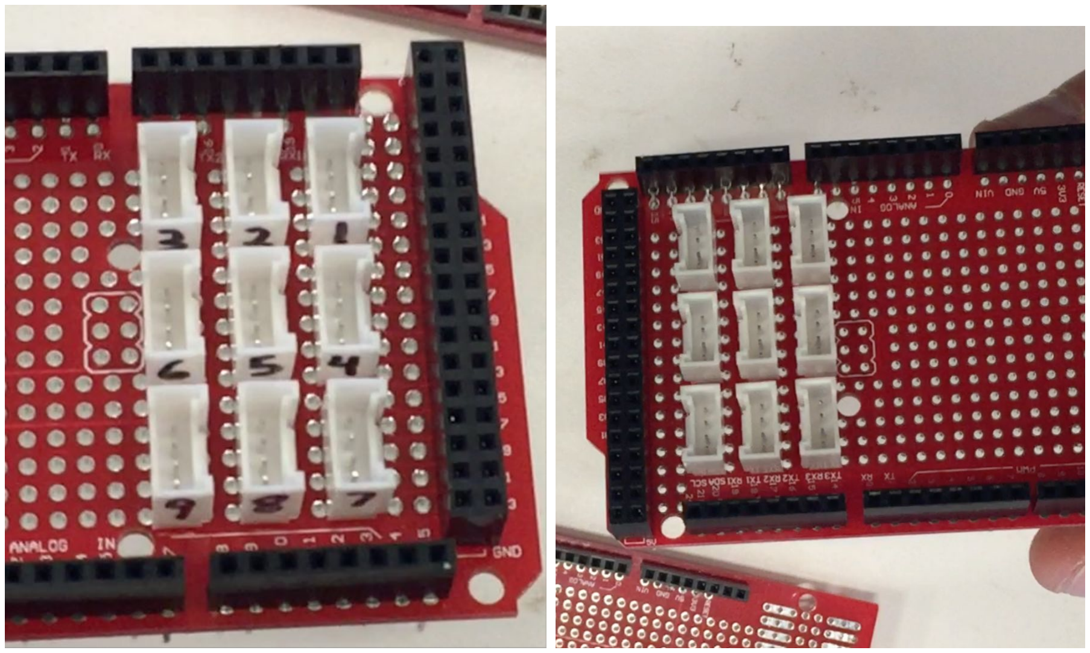
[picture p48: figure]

iv. | Follow the schematic when connecting wires. Tips:
1. Wire wrapping is easier than soldering to the pins on the grove
| connectors. Where multiple connections to a single point are required, try to make the multiconnection point be something that you can wire wrap.
2. If you are unsure what a wire wrapping tool is or how to use it, by
| searching for “wire wrapping electronics tutorial” you will find some good information.
3. As you can see from the schematic, there are a lot of connections
| routed to many different places. This will result in the wires on the

schematic forming a sort of ratsnest. To help manage this complexity, it is recommended you try to color code the wires as best as possible. One schema to do so is:
a. Ground: Black
b. Voltage Source: Red
c. Signal: Else
4. A soldering iron with a fine pointed tip will make the job easier.

### 9. Controller Module

a. Materials
i. Arduino mega 2560
ii. | USB A-to-B cable
iii. | Finished arduino mega protoshield module
iv. | Grove base shield
v. Raspberry Pi 2
vi. | 8 GB SD card
vii. | Raspberry Pi 2 power supply
viii. | 20’ ethernet cable
ix. | Touch screen display
x. 2x13 ribbon cable
xi. | small .5” screws x8
xii. | Reed Reay
b. Tools
i. Hot glue gun
ii. small screwdriver
c. Tools Consumables
i. Hot glue
d. Instructions
i. Screw the arduino into the electronics panel
ii. | Place the perfboard on the arduino mega
iii. | place the grove shield on top of the perfboard
iv. | Screw the raspberry pi into the electronics panel
v. Screw the screen into the acrylic front plate of the food computer and
| connect to the raspberry pi with the ribbon cable
vi. | Load the image onto the SD card and place in the raspberry pi
vii. | Connect the Arduino usb cable to the raspberry pi
viii. | *Note, connect the signal line of the reed relay to pin 22 on the Arduino.
| The power and ground are used to break the connection on the EC
| sensor so that there is not noise when the pH sensor is recording.
| Connect the power and ground of the EC to the power and ground out of
| the reed relay.

### 10. Air Sensors Module

a. Materials
i. Cozir CO2 Sensor
ii. | Grove Digital Light Sensor
iii. | Grove Temperature/Humidity Sensor Module
b. Tools
i. Screwdriver
ii. | small .5” screws
iii. | 1”x1” square of .5” thick pvc
iv. | .75”x2.5” rectangle of .5” thick pvc
v. 1” stamped angle section
vi. double sided foam tape, about 5”x1”
c. Instructions
i. The temp/humidity and light sensors sit between the circulation fan and
| the vent fan louver.
ii. | First start by taping the rectangle of PVC lengthwise to the angle, so that
| the end of the rectangle is flush with the same surface as the angle.
iii. | Next apply tape to the back of the angle and place it so that it is flush with
| the louver and 6” above the lowermost surface of the window to the grow
| chamber.
iv. | Next tape the temperature/humidity center vertically on the front face of
| the angle below the cantilevered PVC rectangle (see below).
v. Next tape the light sensor to the top of the PVC rectangle so that it is at
| the very edge. This ensures that nothing will obstruct light from reaching
| the sensor
vi. | Finally, tape the 1”x1” square of PVC to the back of the CO2 sensor and
| then tape to the electronics panel right above the circulation fan
vii. | Wire the sensors to the ports specified in the schematic

### 11. Lights

a. Materials

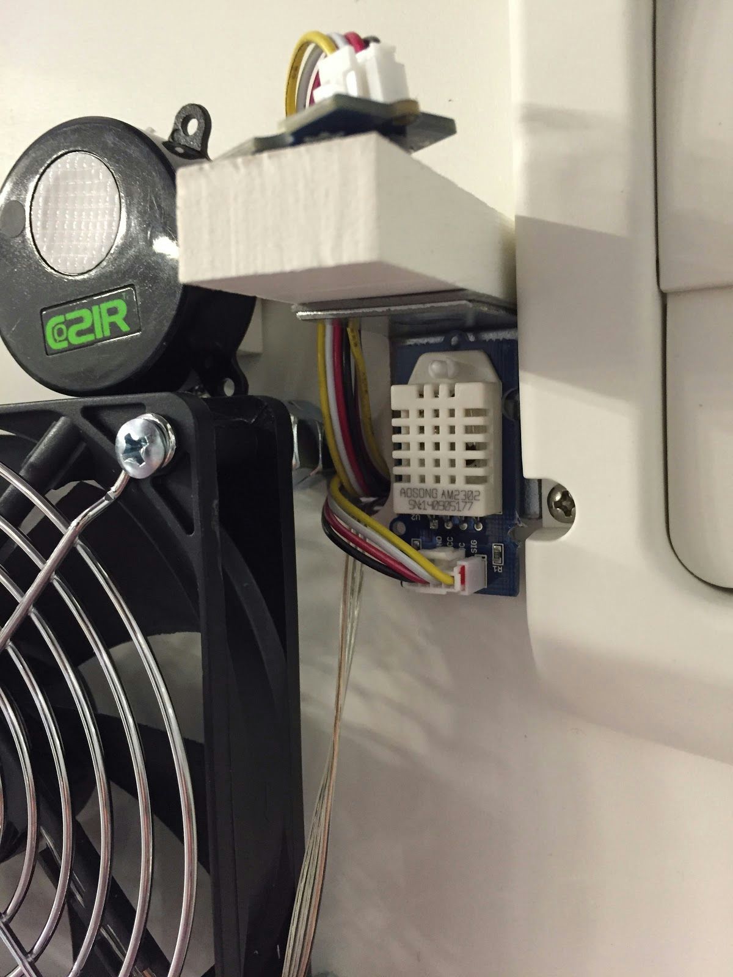
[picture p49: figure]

i. one rope of white LEDs
ii. grove cable
b. Tools
i. Knife
c. Tools Consumables
i. Clear shipping tape
d. Instructions
i. The strip of LEDs will go around the circumference of the electronics
| panel. Starting above the wire management box and wrapping
| counterclockwise, stick the strip to the edge of the PVC. Use intermittent
| clear tape to hold the leds onto the panel.
ii. | As per the schematic, connect the power and ground of the strip to the
| white and yellow wires of a grove connector. The red and black will go to
| the second LED strip on the LED panel assembly.
12. Grow LED Panel and Camera Assembly
a. Materials
i. two grow LED panels
ii. 18” stamped flat
iii. 24” stamped flat
iv. 8” stamped flat v. 19.5” ⅜-16 threaded rod vi. 1.5”x1.5” PVC square
vii. Webcam and wire
viii. small .5” screws
ix. 3” stamped flat
b. Tools
i. ⅜” drill bit
ii. power drill
iii. knife
iv. bandsaw
v. screwdriver
c. Tools Consumables
i. Clear shipping tape
d. Instructions
i. Start with two panels

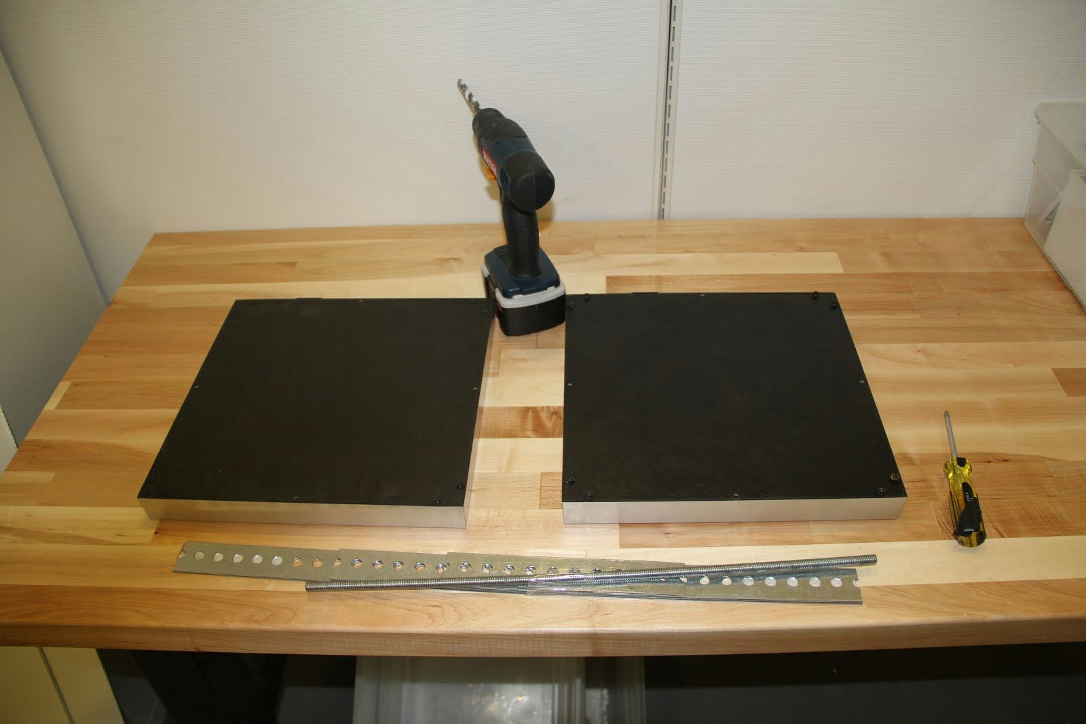
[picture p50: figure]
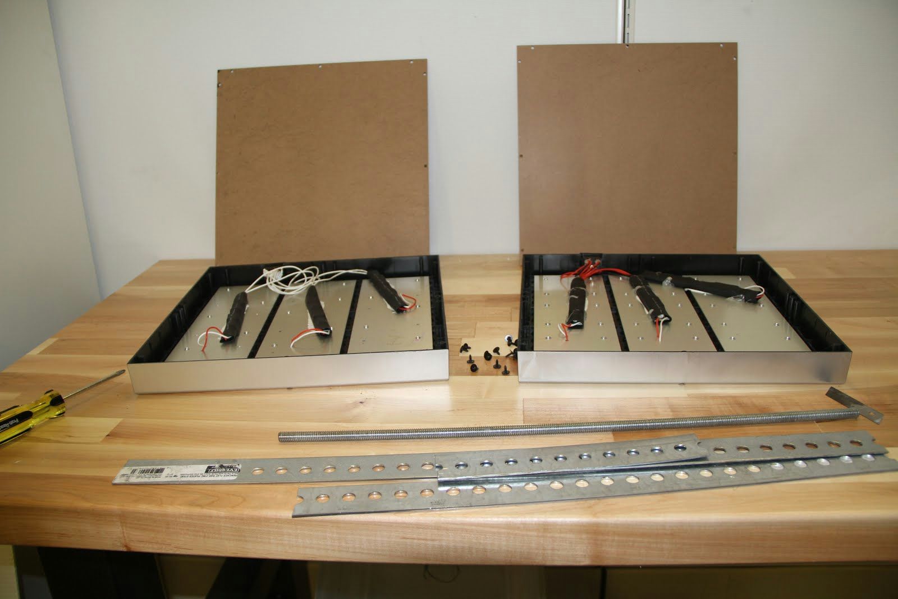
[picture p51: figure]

ii. Unscrew the covers and save the screws iii. Take the 18” section of stamped flat to the shop and cut a tab on either end the width of the hole (⅜”). Sand so that there are no sharp edges.

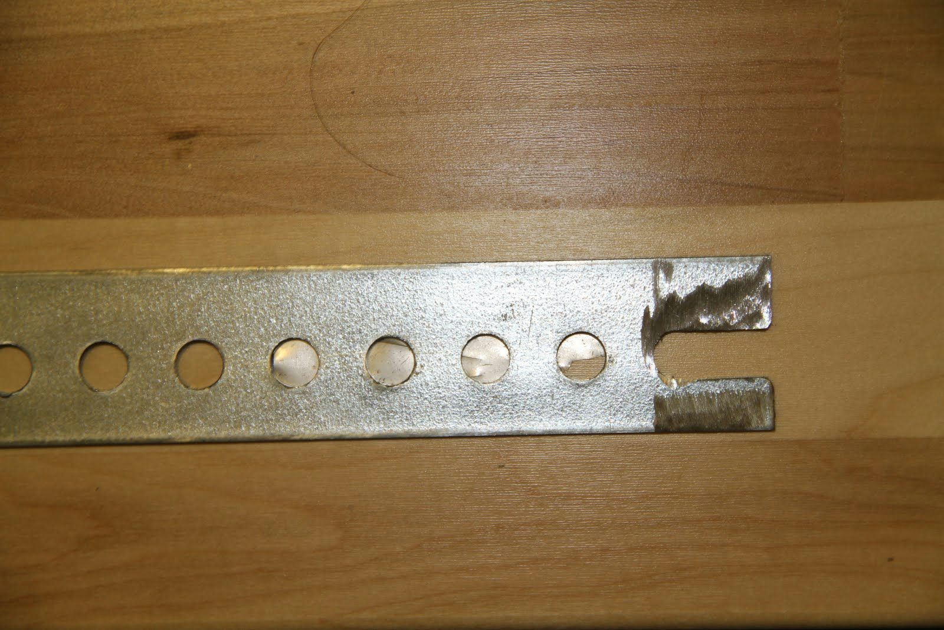
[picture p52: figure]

iv. Align the 18” section with one panel so that the plug is to the right. Drill two holes and bolt the stamped flat to the light plastic enclosure.

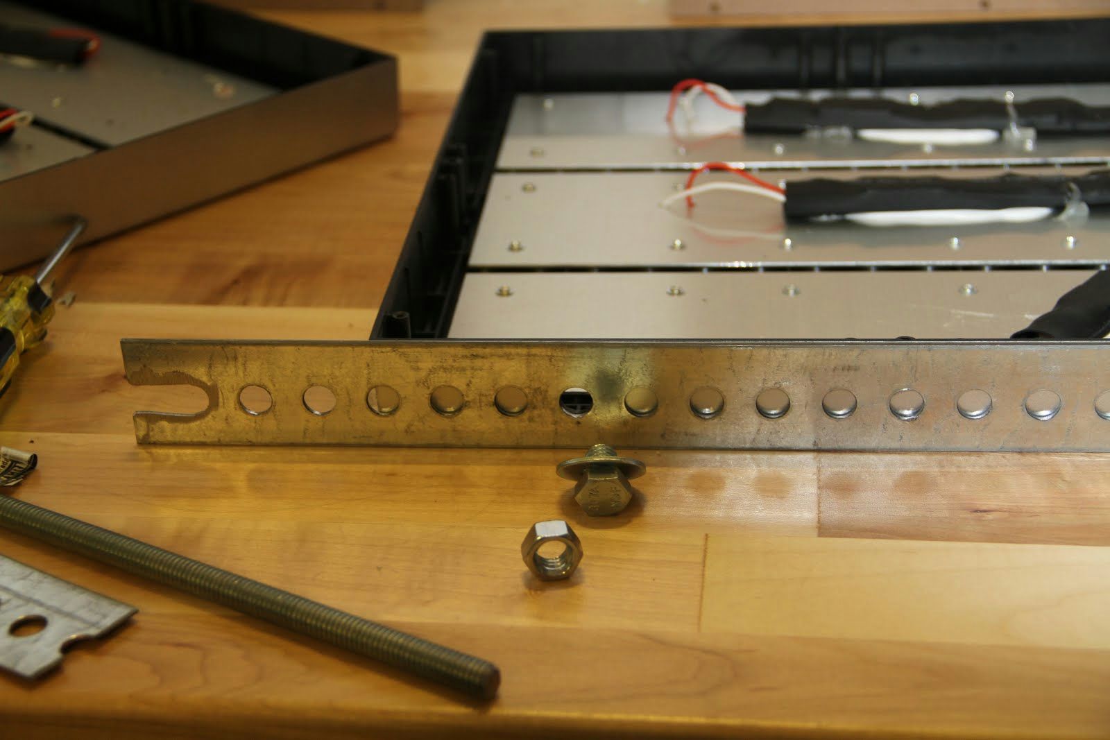
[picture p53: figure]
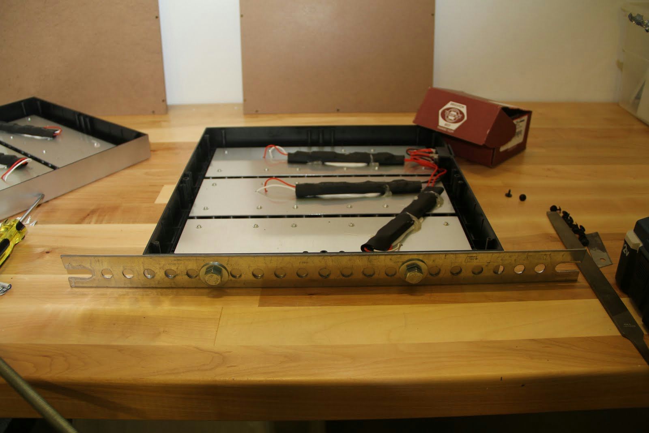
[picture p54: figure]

v. Place a second panel adjacent to the in the orientation below (both plugs facing back) and attach the 24” section to the front face the same way.

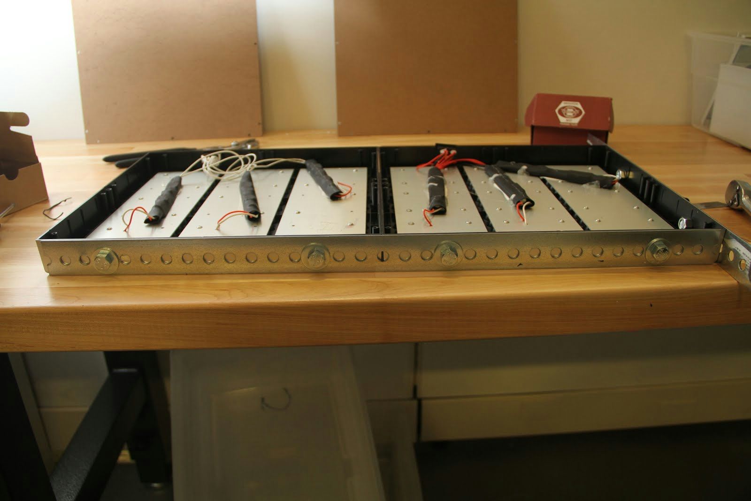
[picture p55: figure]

vi. Take the 8” section and attach to the side with the plugs.

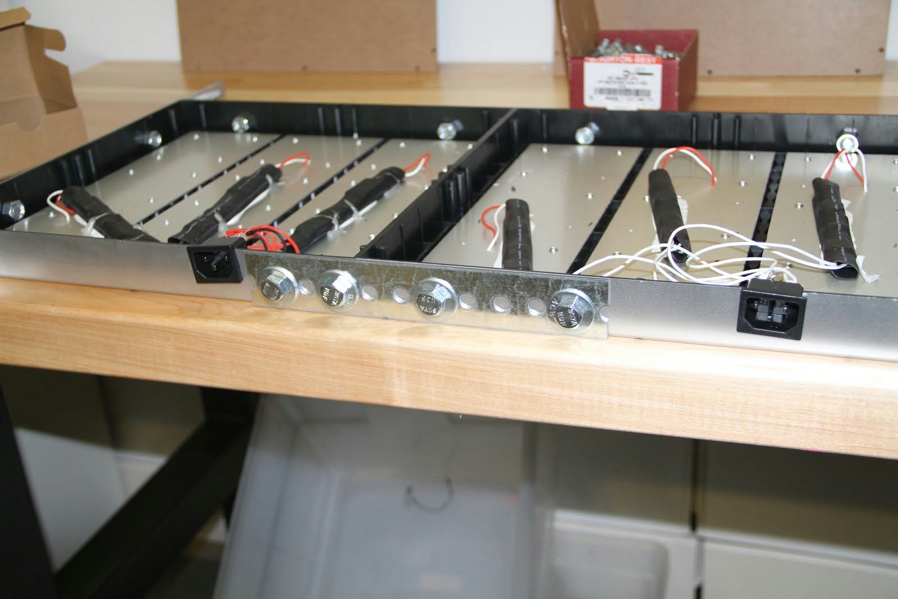
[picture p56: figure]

vii. Drill a hole through the center seam of the two panels. This will be used for the camera mount.

viii. Take the PVC and drill a .75” hole through the center. Drill two small (.125”) holes in the bottom of the 3” stamped flat section

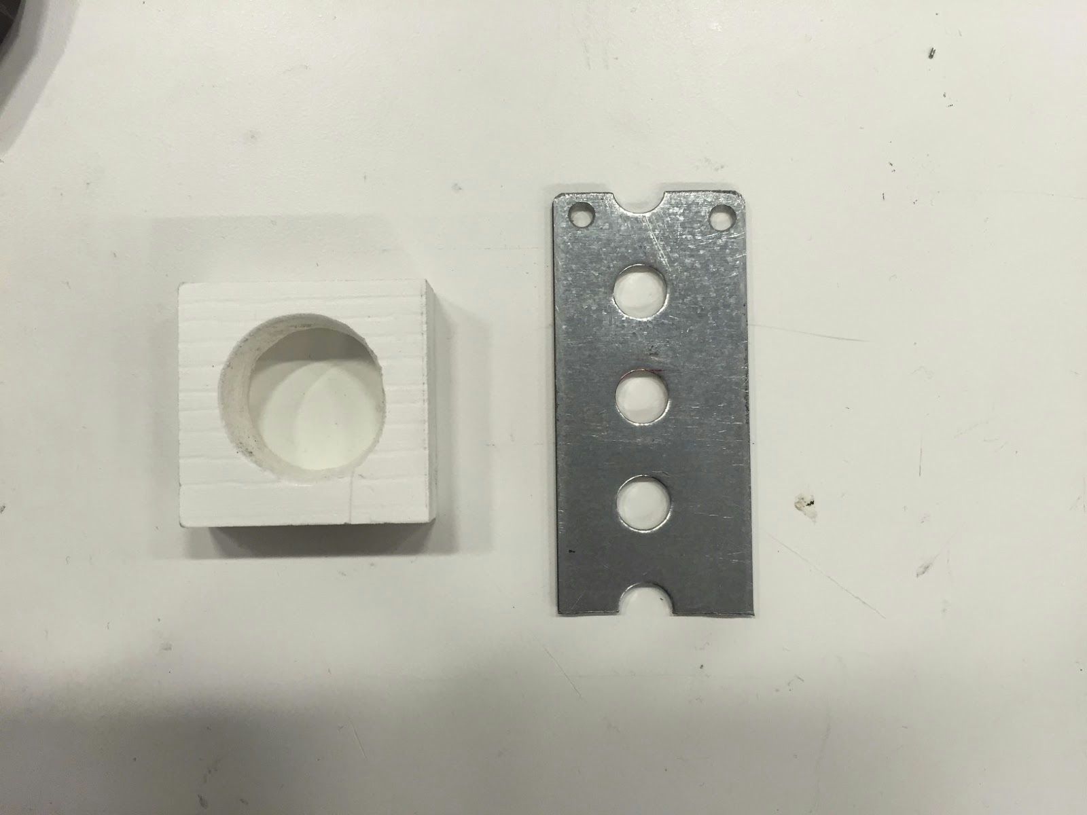
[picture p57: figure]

ix. Clip the corners of the webcam where the mounting holes are. This creates room for the screws. Place the webcam on the PVC block so that the lens goes through the center. Screw through the corners to secure the webcam to the block

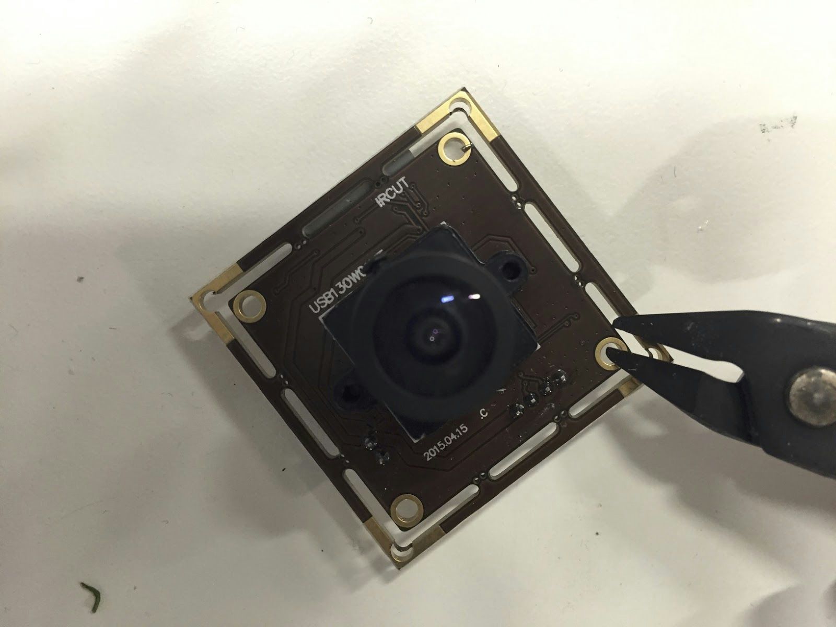
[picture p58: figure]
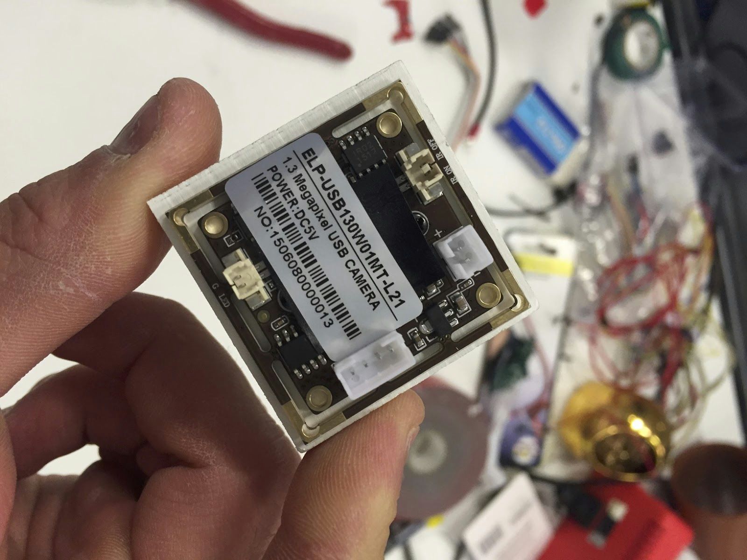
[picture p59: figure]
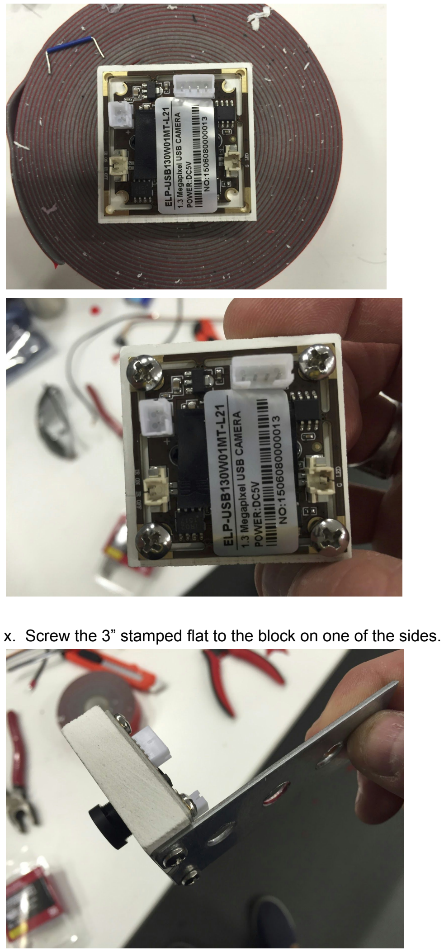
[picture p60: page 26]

x. S

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
xi. Place the webcam assembly through the center so that the uppermost hole on the stamped flat aligns with the center hole through the plastic enclosures. Bolt through all three and tighten. Replace the coverings on each LED panel and it is ready for assembly.

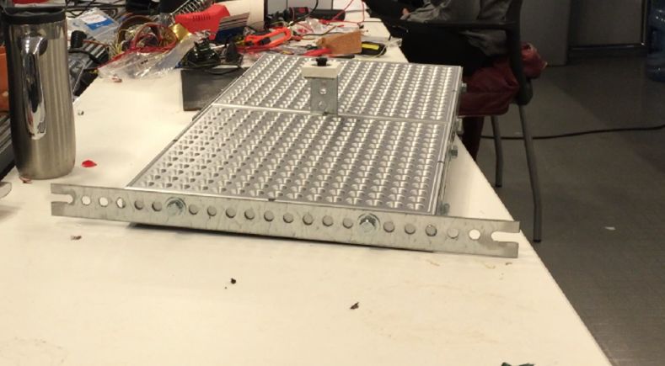
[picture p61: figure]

xii. Assemble the support rod. Screw a nut from each edge of the rod 5” in. Place a washer and second nut and tighten. Place one more nut on each side and thread through the frame. Tighten with nuts on the outermost edge. This is what the front of the lights rests on.

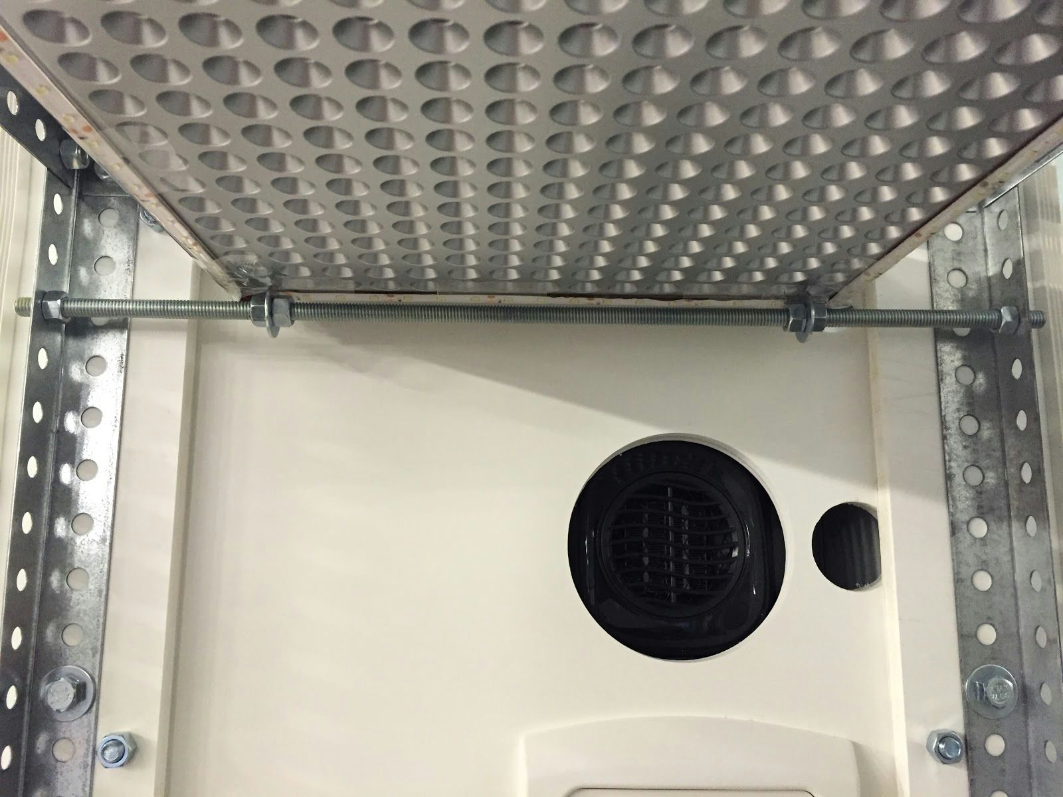
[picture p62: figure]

The tabs are used to hold the other side of the lights to the frame.

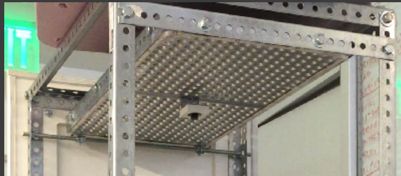
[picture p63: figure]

Finally lay a strip of leds on the face of the led panel. Extend the LED wires and pass them through the hole in the electronics panel upper corner. Connect to the black and red wires of the other LED grove connector. Place both in port S2.
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

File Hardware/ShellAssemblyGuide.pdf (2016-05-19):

Cutting the Insulation Foam

If you are cutting using a standard table saw, I found that it is easier to cut the large 4’x8’ sheet into sections slightly larger than the ultimate panel dimensions. This both makes each individual panel easier to work with and provides a clean opposite to the final cut width.


Once the sheets has been cut into the approximate panel dimensions, you can then cut the actual dimensions in the CAD.

Front Panel: 25.6875” x 30.625”
Back Panel: 25.6875” x 30.625”
Side Panel: 19.375” x 30.625”
Top Panel: 21.375” x 25.6875”

Next you need to cut the window into the front panel. I created a jig but a ruler works just fine. From the upper left corner as the origin of a cartesian system, measure 3.25” in the +x direction and 3.1875 in the y direction. This will be the upper left corner of the window. The dimensions of the window are 18.75” wide by 19.3125” tall. See picture below for relative orientation if confused. Cut out the window and discard the scrap.


Front Panel, Back Panel, Side Panel, and Top Panel

Gluing Together the Foam Box

*Follow the video and consult the CAD for better visuals on how to assemble the box

Using hot glue, lay down a continuous zigzagging line about an inch wide along one of the edges to be glued.


Firmly push the mating panels together and hold while the glue dries. The front and back panels should be on the outermost face, while the side panel sits between the front and back panels. The top panel should be placed on the top of the front, side, and back panels.


Taping the Edges

Once the box has been glued together, the exposed edges where the yellow insulation foam can be seen need to be covered up. Using foil tape, cover all exposed edges so that no foam can be seen.


Cutting the Corruplast

Because the panel dimensions of the corruplast are larger than the foam, cutting approximate dimensions is not possible. In fact, the width dimensions of the panels add up perfectly to 8’ or 96”. So cutting along the exact lines is the only way to make use of the whole panel. Note, due to the width of the saw blade, each panel will be missing between 1/16” ⅛” of material. This has not been a problem for us though.


The exact dimensions are as follows:

Front Panel: 26.625” x 32.5625” Back Panel: 26.625” x 32.5625”
Side Panel: 21.375” x 32.5625”
Top Panel: 21.375” x 26.4375”
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

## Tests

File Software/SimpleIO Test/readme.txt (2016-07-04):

This folder (SimpleIO) contains simple Arduino sketch and Python based GUI
to test all UART communications, sensors, and actuators operations.
Both drafts are far from perfect, it is meant for quick hardware/software test.
Might be full of bugs. Definitely needs improvement.

For Arduino:
-Just upload the sketch normally.

To run the GUI:
-Install Python 2.7
-Install PyQt 4
-Install pySerial
-run main.py
-optional: install pyCharm
-if run on raspberryPi: change the COM5 into /dev/ttyACM0

Sensors used:
(software uart) http://www.co2meter.com/products/cozir-0-2-co2-sensor
(DHT22) https://www.seeedstudio.com/item_detail.html?p_id=838
(I2C) https://www.seeedstudio.com/item_detail.html?p_id=1281
(ADC) http://www.dfrobot.com/index.php?route=product/product&product_id=1025#.V2vjyPkrKHs
(ADC and onewire) http://www.dfrobot.com/index.php?route=product/product&product_id=1123#.V2vrN_krKHu

The Arduino sketch designed so that it can be run on either uno or mega (cost optimisation).

The Python GUI designed in PyQt Designer (auto generated).
I learn it from here:
https://www.youtube.com/watch?v=Dmo8eZG5I2w&list=PLQVvvaa0QuDdVpDFNq4FwY9APZPGSUyR4&index=16

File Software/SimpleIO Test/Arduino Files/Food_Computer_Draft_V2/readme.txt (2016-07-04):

Same as draft V1. Rewrote to use classes for easier documentation.

Updated pin definitions.

All sensors have arrived and included in the code.
EC sensor was calibrated. pH readings are not calibrated yet.

All Sensor readings now uses float for uniformity.

All included libraries comes with links to its sources.

To do: Doxygen.

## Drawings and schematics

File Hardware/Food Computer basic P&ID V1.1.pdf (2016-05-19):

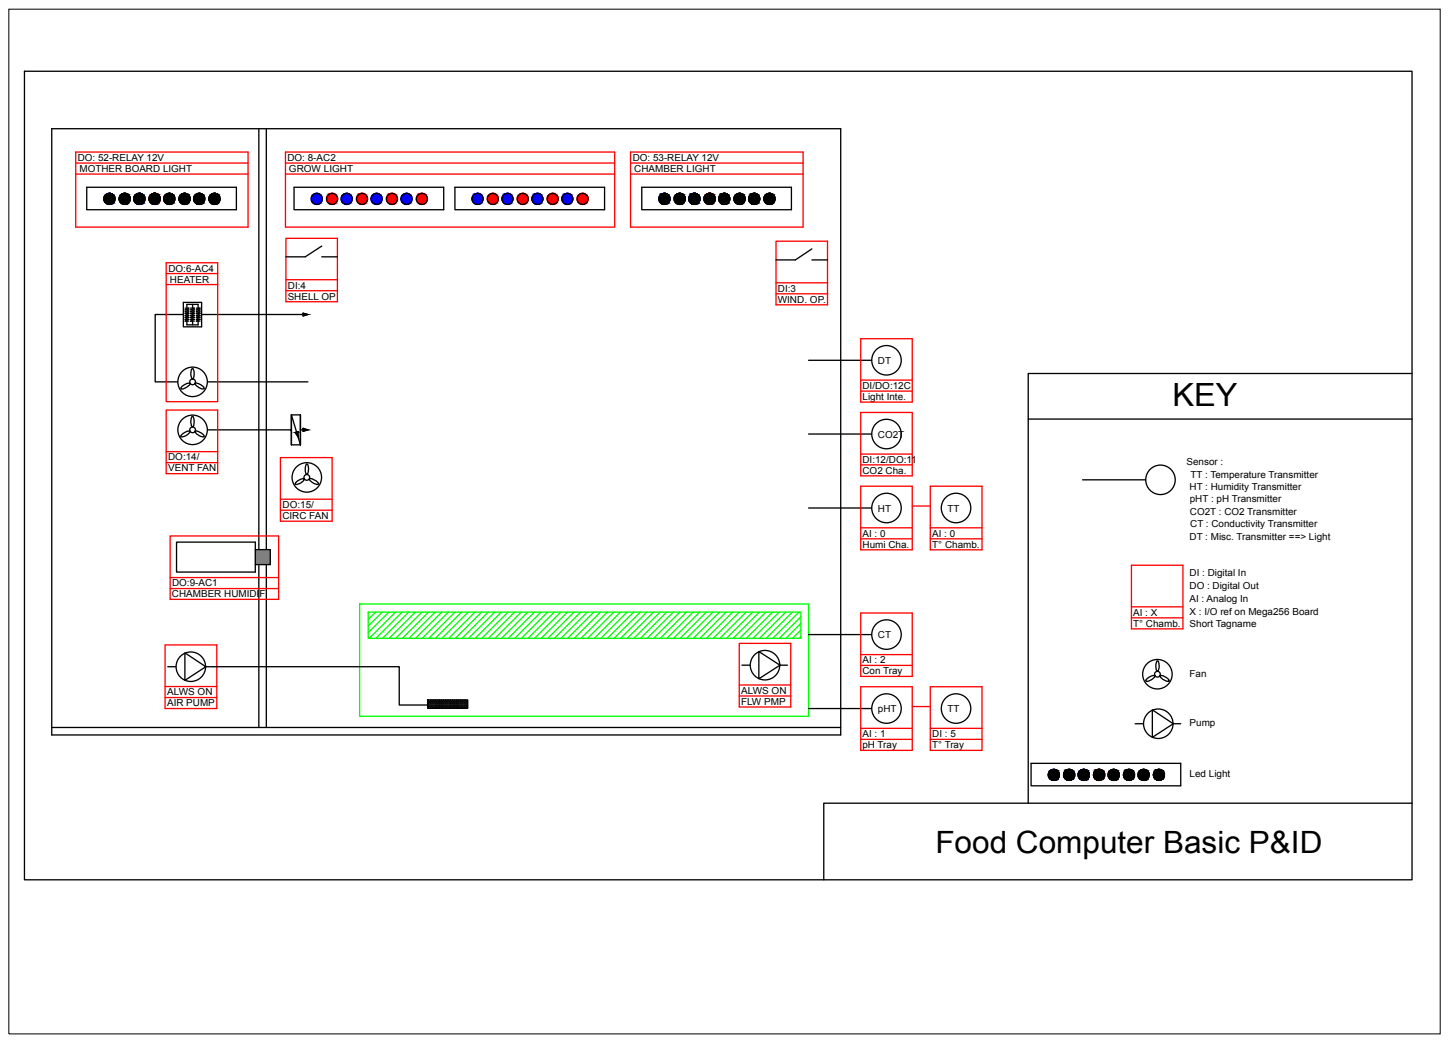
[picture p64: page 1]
VENT FAN; CIRC FAN; AIR PUMP; ALWS ON; FLW PMP; GROW LIGHT; pH Tray; CHAMBER LIGHT; DO: 53-RELAY 12V; Con Tray; T° Tray; Humi Cha.; CO2 Cha.; Light Inte.; T° Chamb.; SHELL OP; WIND. OP.; Led Light

DO: 52-RELAY 12V
MOTHER BOARD LIGHT

Sensor :
TT : Temperature Transmitter
HT : Humidity Transmitter
pHT : pH Transmitter
CO2T : CO2 Transmitter
CT : Conductivity Transmitter
DT : Misc. Transmitter ==> Light

DI : Digital In
DO : Digital Out
AI : Analog In
X : I/O ref on Mega256 Board
Short Tagname

DO:9-AC1
CHAMBER HUMIDIF

Food Computer Basic P&ID

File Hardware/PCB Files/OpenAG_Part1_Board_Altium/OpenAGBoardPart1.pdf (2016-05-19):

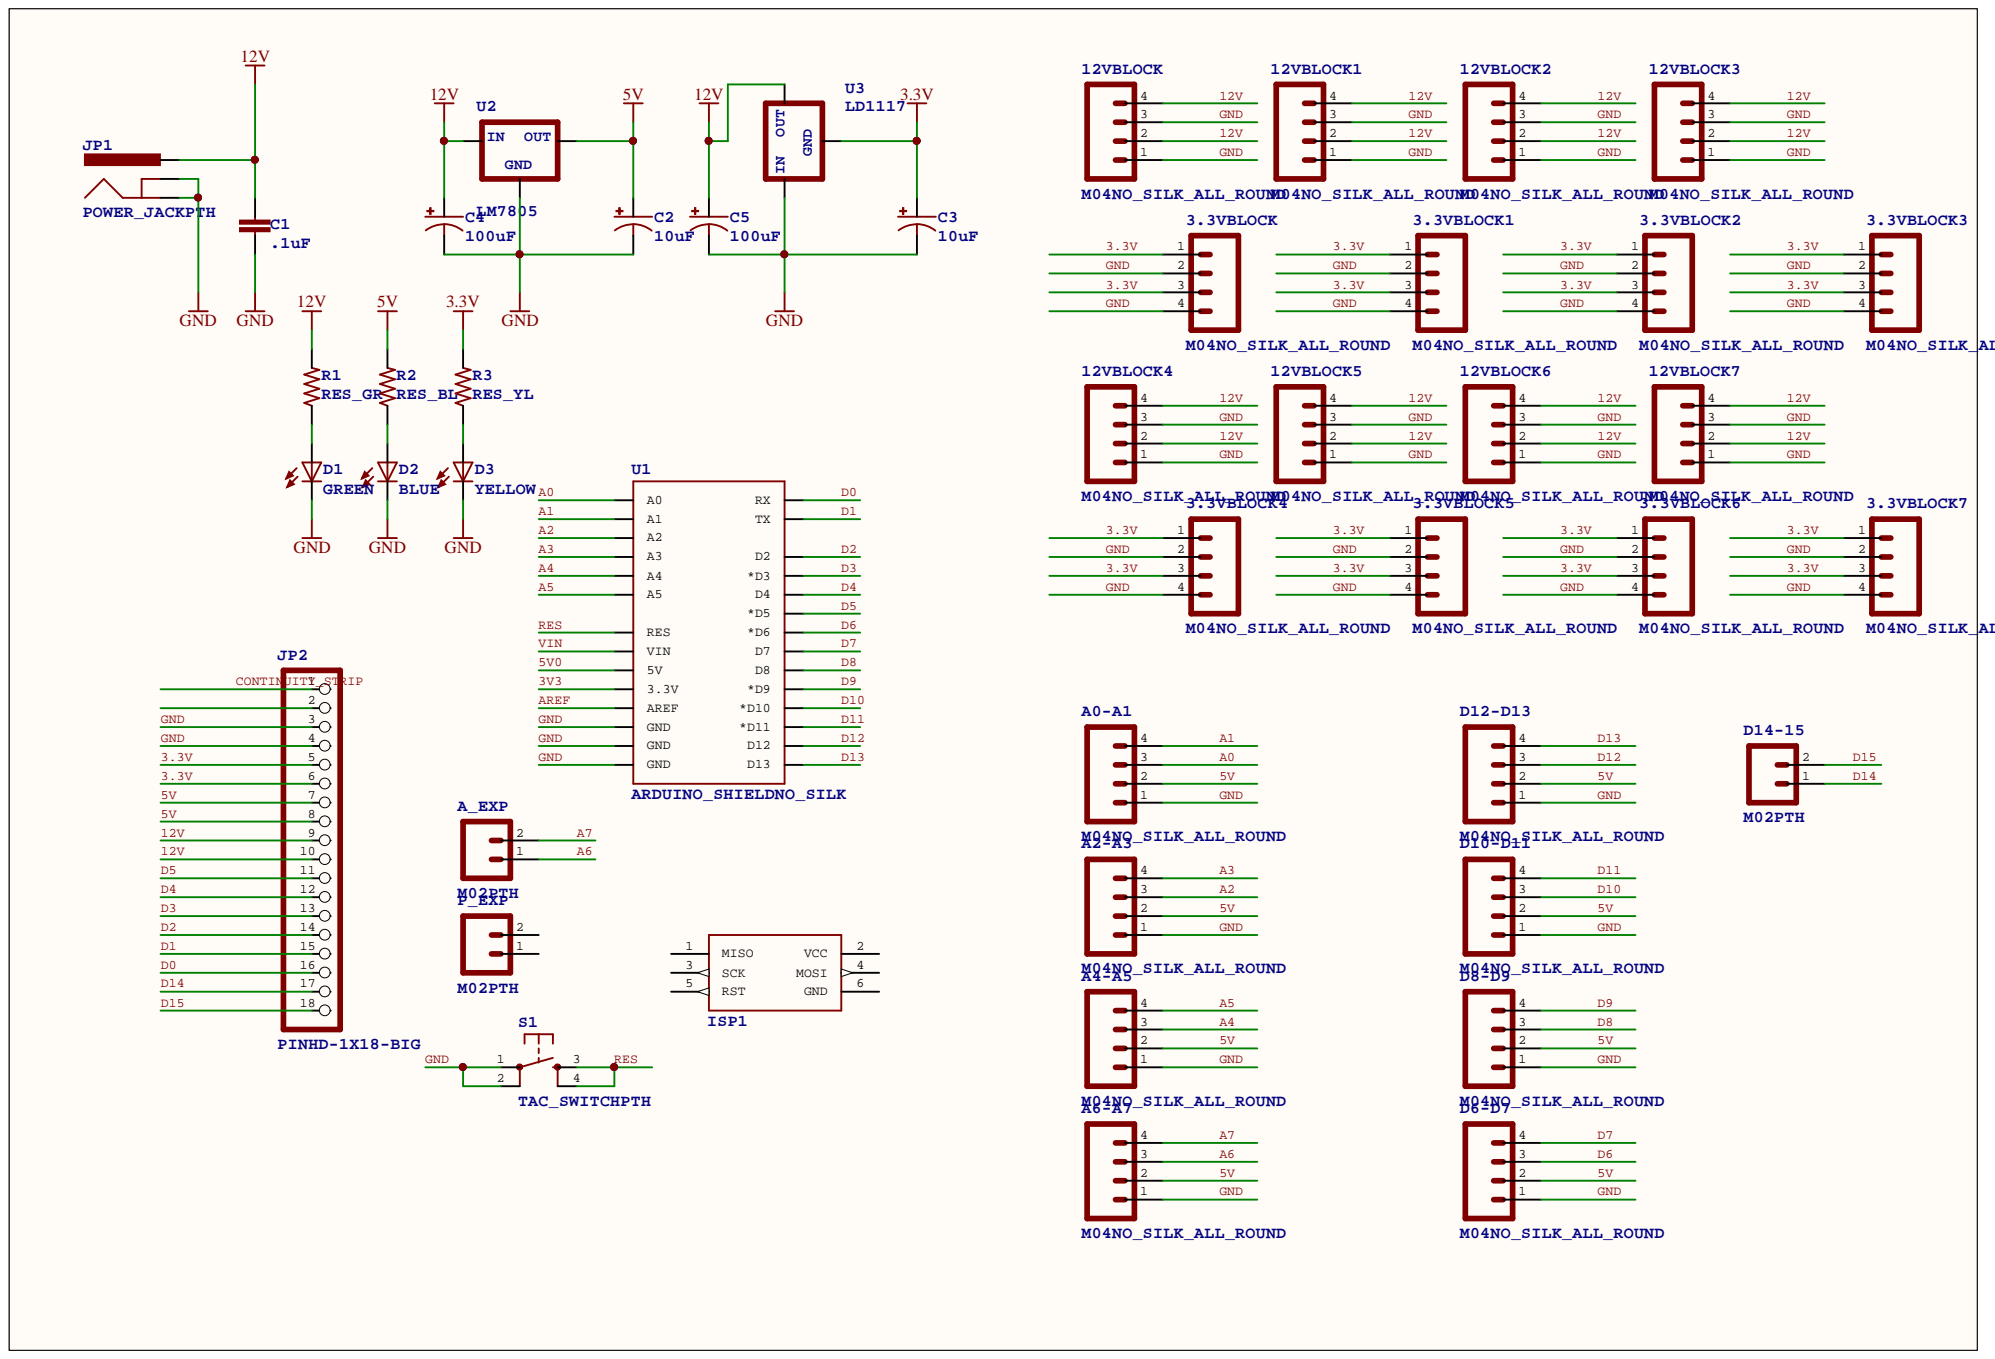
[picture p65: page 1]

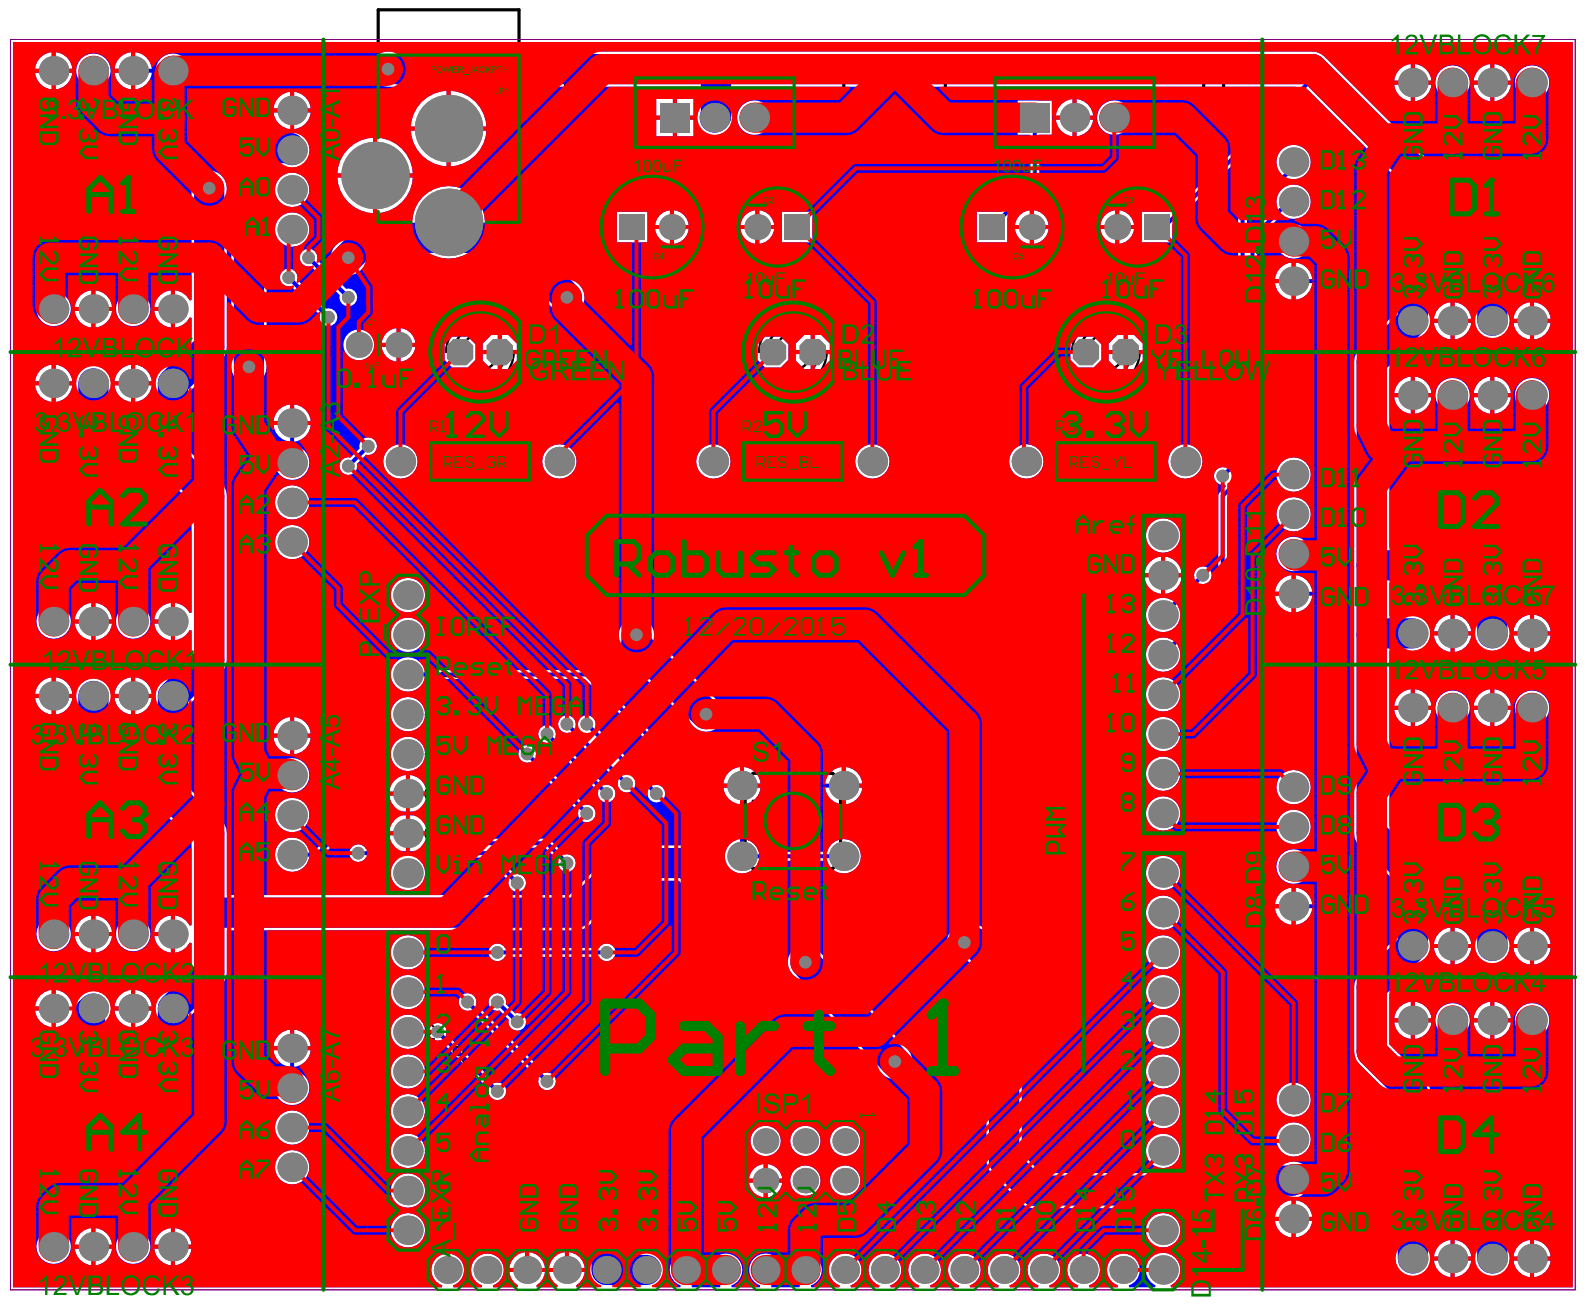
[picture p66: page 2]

Comment M04NO_SIL K_ALL_ROU ND | 4Standard 4-Header Description pin 0.1" header. Use with straight break away headers (SKU : PRT-00116), right angle break away headers (PRT-00553), swiss pins (PRT-00743), machine pins (PRT-00117), and female headers (PRT-00115). Molex polarized connector foot print use with SKU : PRT-08231 with associated crimp pins and housings. 1MM SMD Standard 2- | Designator 3.3VBLOCK, 3.3VBLOCK1, 3.3VBLOCK2, 3.3VBLOCK3, 3.3VBLOCK4, 3.3VBLOCK5, 3.3VBLOCK6, 3.3VBLOCK7, 12VBLOCK, 12VBLOCK1, 12VBLOCK2, 12VBLOCK3, 12VBLOCK4, 12VBLOCK5, 12VBLOCK6, 12VBLOCK7, A0-A1, A2-A3, A4-A5, A6-A7, D6-D7, D8-D9, D10-D11, D12-D13 | Footprint 1X04_NO_SI LK_ALL_ROU ND | LibRef M04NO_SIL K_ALL_ROU ND | Quantity | 24

M02PTH | pin 0.1" header. Use with -straight break away headers ( PRT-00116) -right angle break away headers (PRT-00553) -swiss pins (PRT-00743) -machine pins (PRT-00117) -female headers (PRT-00115) Molex polarized connector foot print use with: PRT-08233 with associated crimp pins and housings. 2.54_SCREW TERM for | A_EXP, D14-15, P_EXP | 1X02 | M02PTH | 3

.1uF | CapacitorSta ndard 0603 ceramic capacitor, and 0.1" leaded capacitor. | C1 | CAP-PTH-SMALL | CAPPTH | 1

10uF | Capacitor PolarizedThe se are standard SMD and PTH capacitors. Normally 10uF, 47uF, and 100uF in electrolytic and tantalum varieties. Always verify the external diameter of the through hole cap, it varies with capacity, voltage, and manufacture r. The EIA devices should be standard. | C2, C3 | CPOL-RADIAL-10UF-25V | CAP_POLPT H2 | 2

100uF | Capacitor PolarizedThe se are standard SMD and PTH capacitors. Normally 10uF, 47uF, and 100uF in electrolytic and tantalum varieties. Always verify the external diameter of the through hole cap, it varies with capacity, voltage, and manufacture r. The EIA devices should be standard. LED | C4, C5 | CPOL-RADIAL-100UF-25V | CAP_POLPT H1 | 2

GREEN | OSRAM: -CHIPLED LG R971, LG N971, LY N971, LG Q971, LY Q971, LO R971, LY R971 LH N974, LH R974 LS Q976, LO Q976, LY Q976 LO Q996 -Hyper CHIPLED LW Q18S LB Q993, LB Q99A, LB R99A -SideLED LS A670, LO A670, LY A670, LG A670, LP A670 LB A673, LV A673, LT A673, LW A673 LH A674 LY LED | D1 | LED5MM | LED5MM | 1

BLUE | OSRAM: -CHIPLED LG R971, LG N971, LY N971, LG Q971, LY Q971, LO R971, LY R971 LH N974, LH R974 LS Q976, LO Q976, LY Q976 LO Q996 -Hyper CHIPLED LW Q18S LB Q993, LB Q99A, LB R99A -SideLED LS A670, LO A670, LY A670, LG A670, LP A670 LB A673, LV A673, LT A673, LW A673 LH A674 LY LED | D2 | LED5MM | LED5MM | 1

YELLOW | OSRAM: -CHIPLED LG R971, LG N971, LY N971, LG Q971, LY Q971, LO R971, LY R971 LH N974, LH R974 LS Q976, LO Q976, LY Q976 LO Q996 -Hyper CHIPLED LW Q18S LB Q993, LB Q99A, LB R99A -SideLED LS A670, LO A670, LY A670, LG A670, LP A670 LB A673, LV A673, LT A673, LW A673 LH A674 LY | D3 | LED5MM | LED5MM | 1

AVRISP-6 | AVR ISP HEADER Standard 6 pin header for AVR programmin g | ISP1 | AVRISP | AVRISP-6 | 1

POWER_JAC KPTH | Power JackThis is the standard 5.5mm barrel jack for power. The PTH is the most common, proven, reliable, footprint. The Slot footprint only works if the mill layer is transmitted to the PCB fab house so be warned. Mating wall wart : TOL-00298 (and others) | JP1 | POWER_JAC K_PTH | POWER_JAC KPTH | 1

PINHD-1X18-BIG | PIN HEADER | JP2 | 1X18-BIG | PINHD-1X18-BIG | 1

RES_GR | ResistorBasi c schematic elements and footprints for 0603, 1206, and PTH resistors. | R1 | AXIAL-0.4 | RESISTORPT H-1/4W | 1

RES_BL | ResistorBasi c schematic elements and footprints for 0603, 1206, and PTH resistors. | R2 | AXIAL-0.4 | RESISTORPT H-1/4W | 1

RES_YL | ResistorBasi c schematic elements and footprints for 0603, 1206, and PTH resistors. | R3 | AXIAL-0.4 | RESISTORPT H-1/4W | 1

TAC_SWITC HPTH | Momentary Switch Button commonly used for reset or general input. Spark Fun Electronics SKU : COM-00097 SMT-SWCH-08247 | S1 | TACTILE-PTH | TAC_SWITC HPTH | 1

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

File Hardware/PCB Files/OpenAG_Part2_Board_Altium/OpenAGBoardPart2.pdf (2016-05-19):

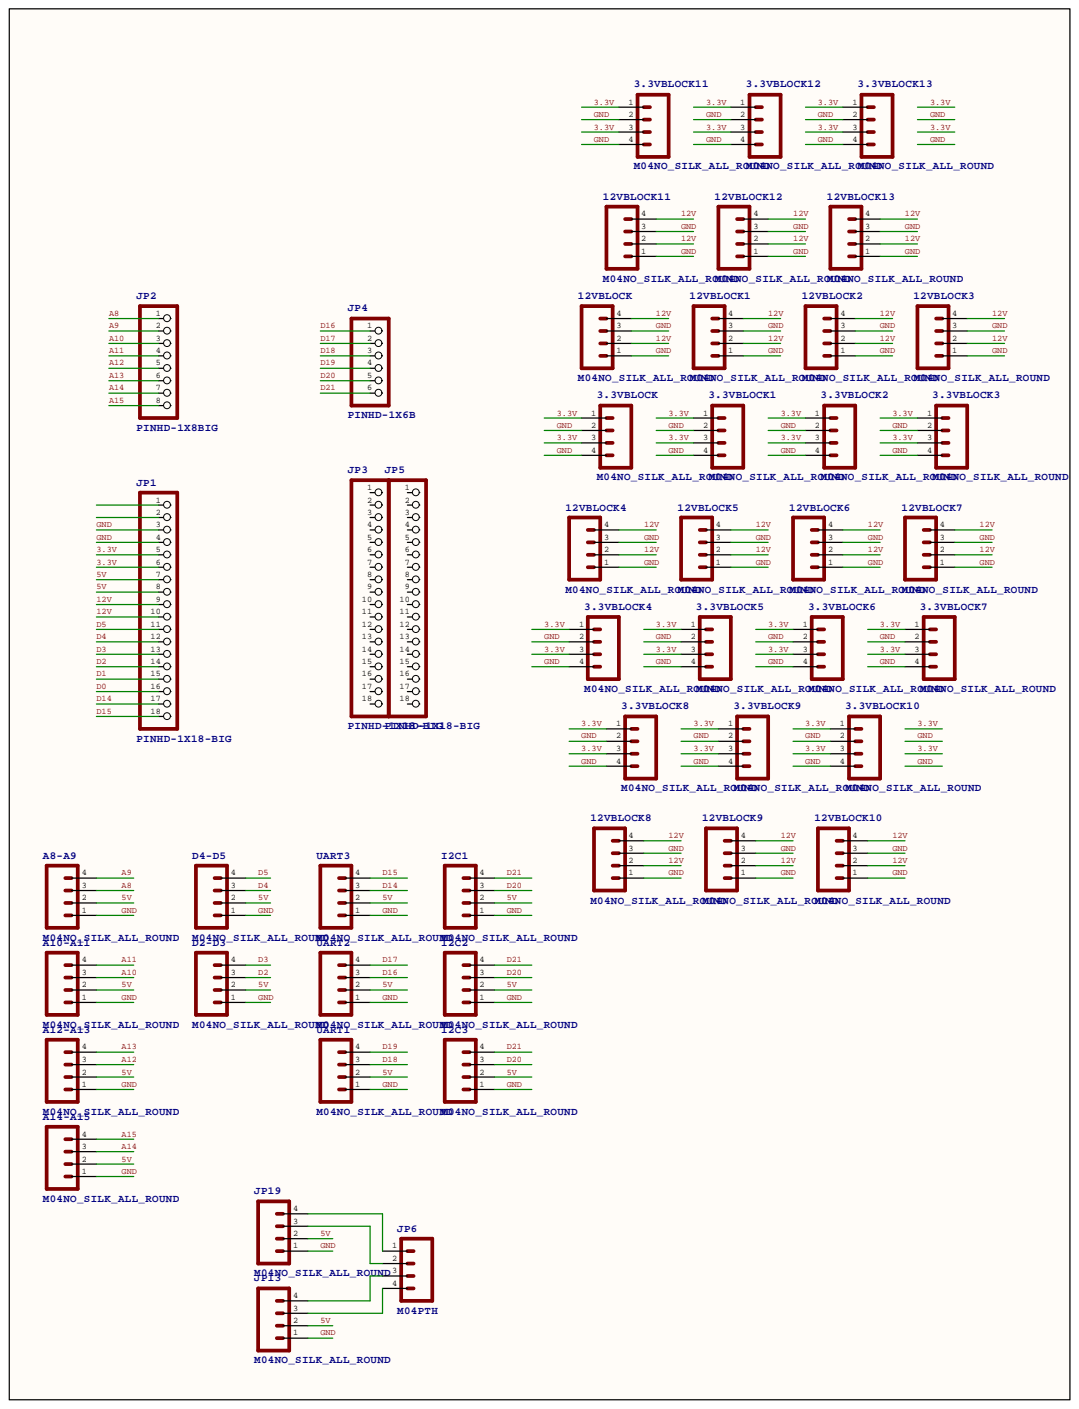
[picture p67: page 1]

JP2 | 3.3VBLOCK11 | | 3.3VBLOCK12 | | 3.3VBLOCK13

3 GND | | 3 GND | | 3 GND
2 12V | | 2 12V | | 2 12V
1 GND | | 1 GND | | 1 GND

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

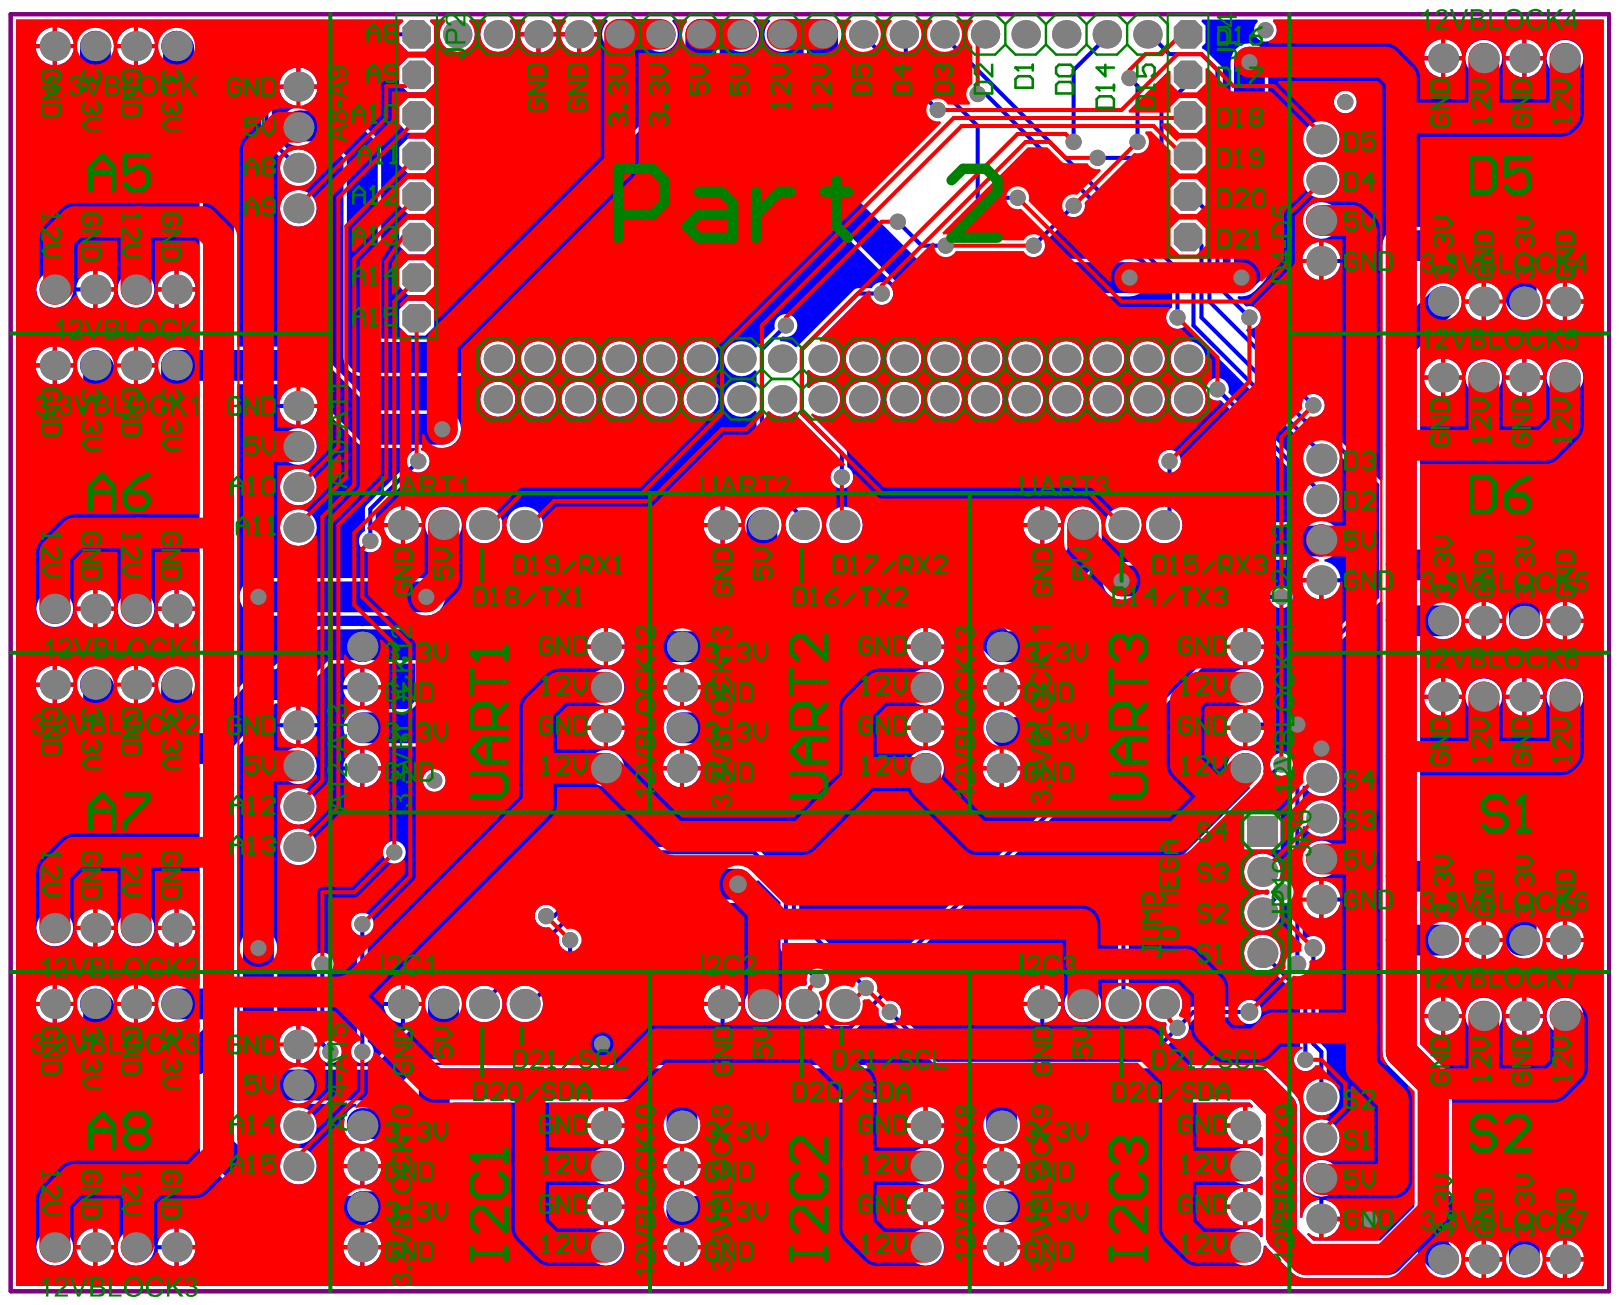
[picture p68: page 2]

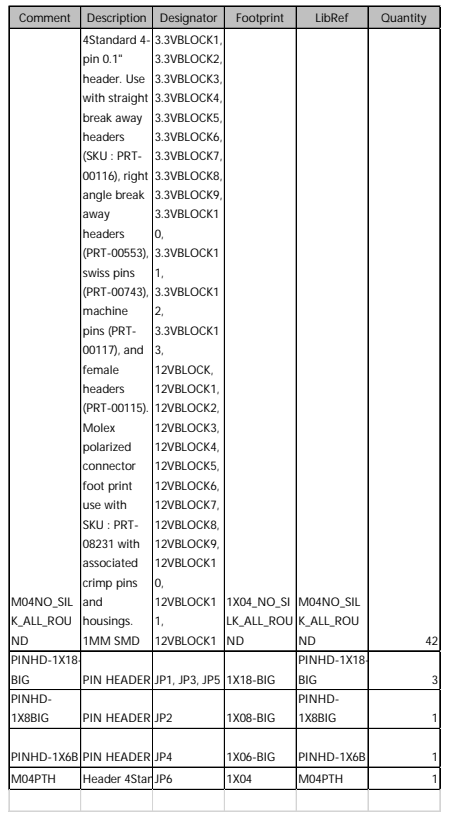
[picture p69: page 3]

PINHD-1X18-BIG | PIN HEADER | JP1, JP3, JP5 | 1X18-BIG | PINHD-1X18-BIG | 3

PINHD-1X8BIG | PIN HEADER | JP2 | 1X08-BIG | PINHD-1X8BIG | 1

PINHD-1X6B | PIN HEADER | JP4 | 1X06-BIG | PINHD-1X6B | 1

M04PTH | Header 4StandJP6 | | 1X 04 | M0 4P TH | 1

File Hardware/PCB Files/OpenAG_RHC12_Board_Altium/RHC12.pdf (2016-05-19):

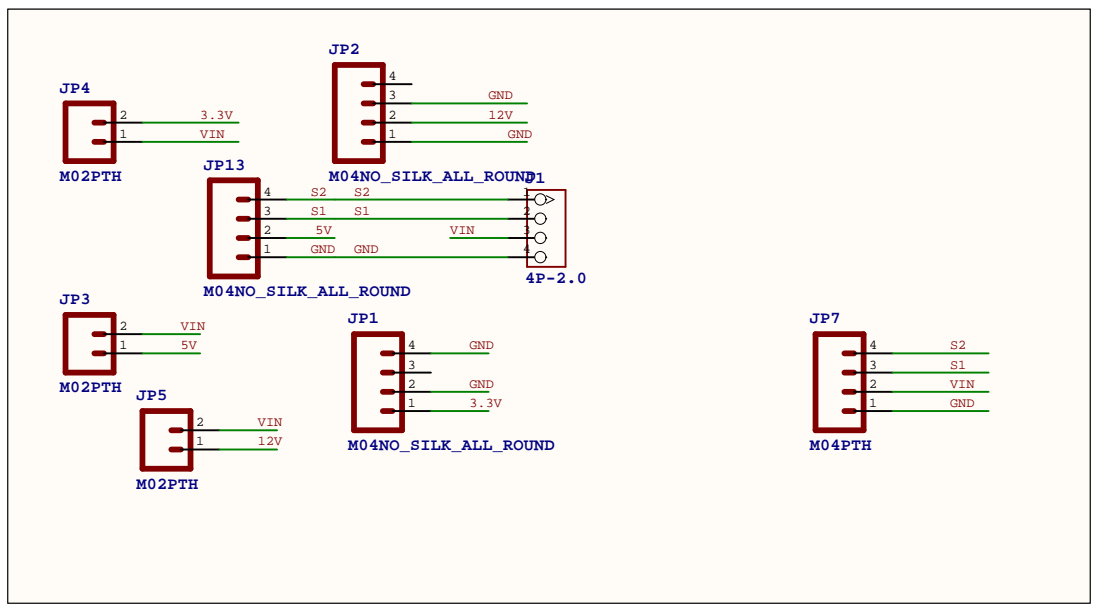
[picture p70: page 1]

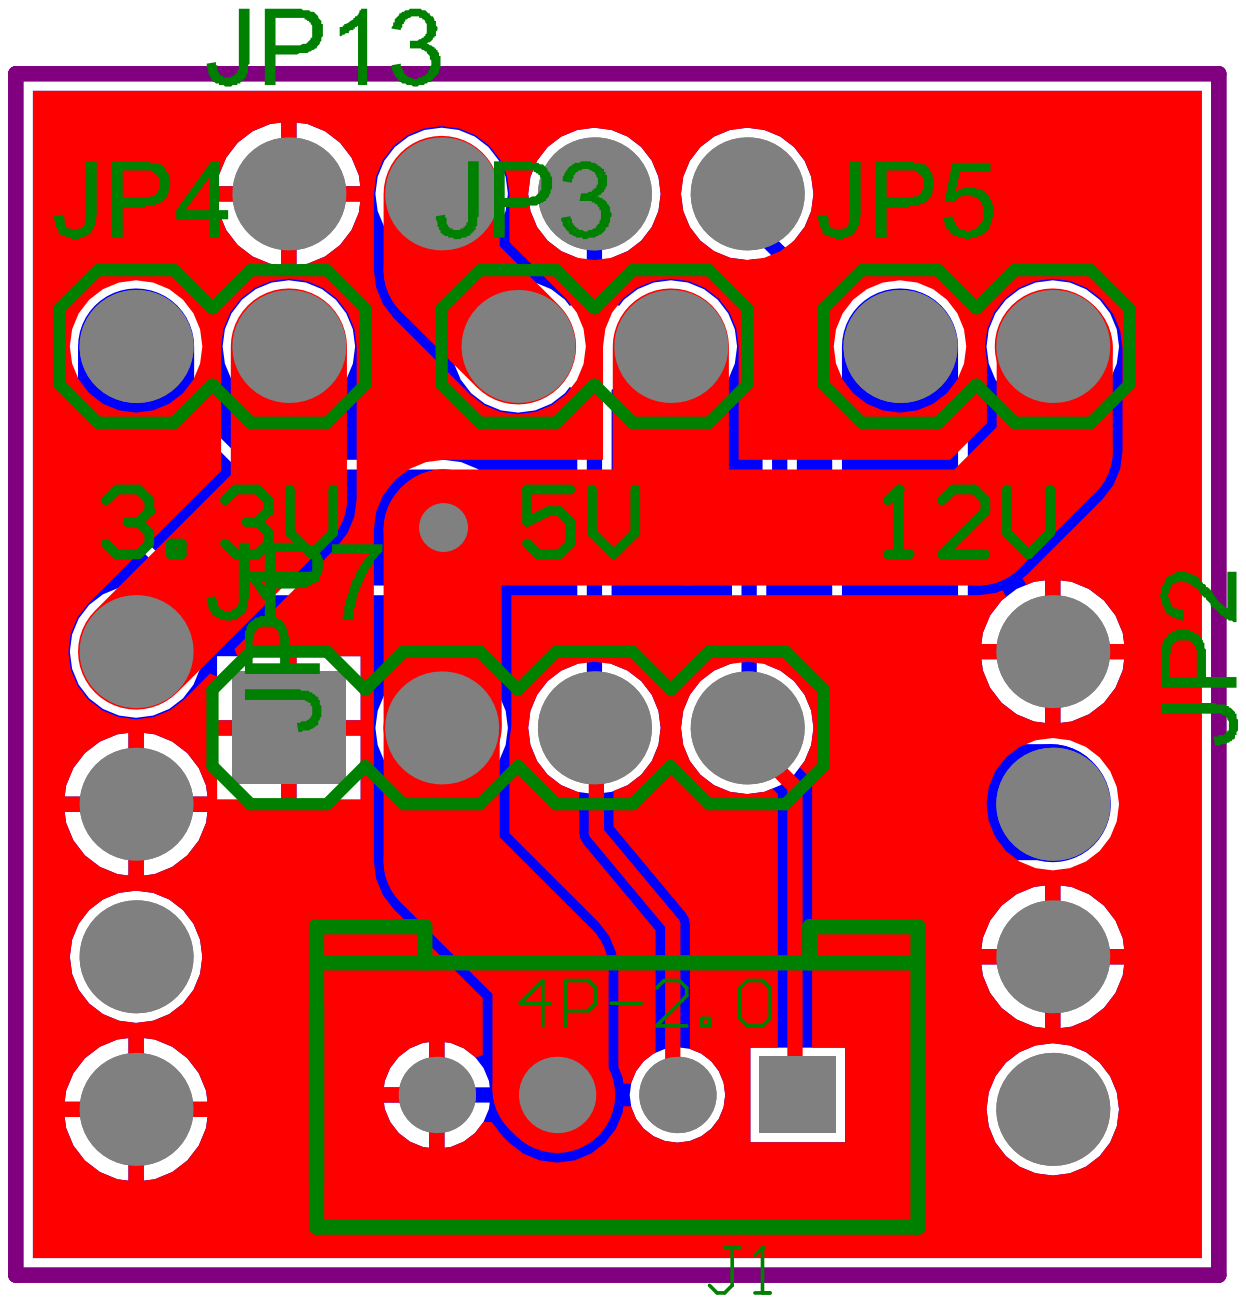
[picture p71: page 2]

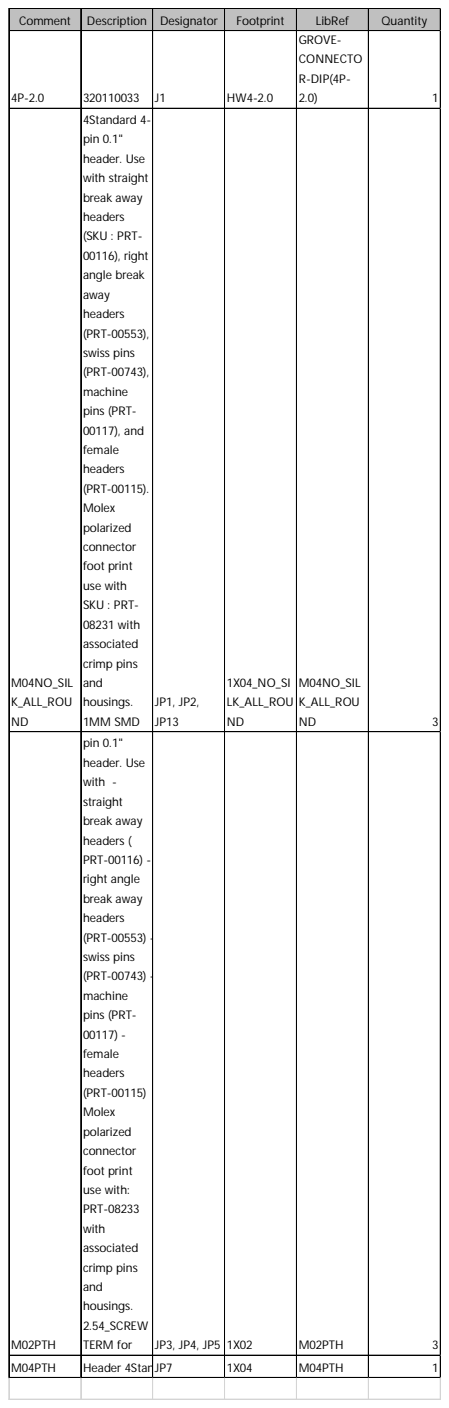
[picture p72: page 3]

Comment | Description | Designator | Footprint | LibRef | Quantity
4P-2.0 | 320110033 | J1 | HW4-2.0 | GROVE-CONNECTO R-DIP(4P-2.0) 1

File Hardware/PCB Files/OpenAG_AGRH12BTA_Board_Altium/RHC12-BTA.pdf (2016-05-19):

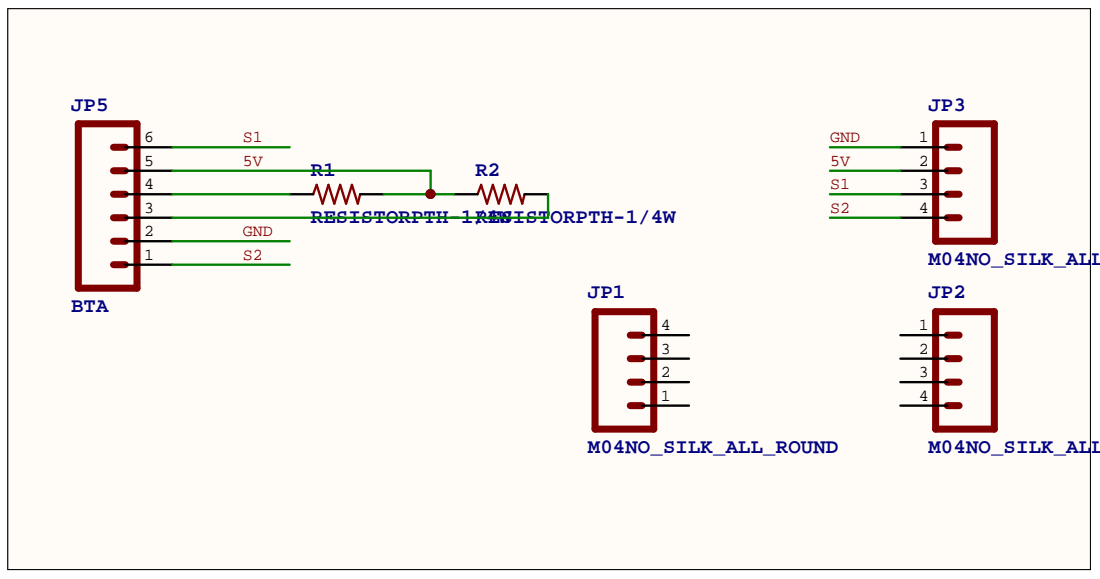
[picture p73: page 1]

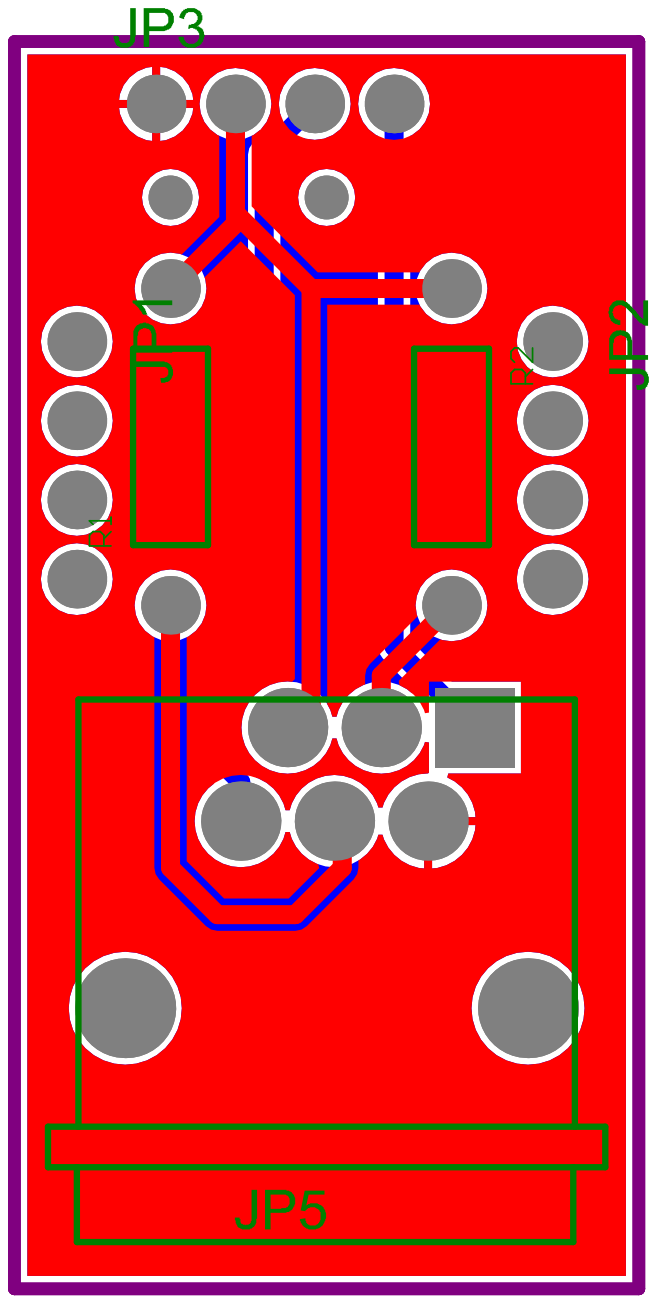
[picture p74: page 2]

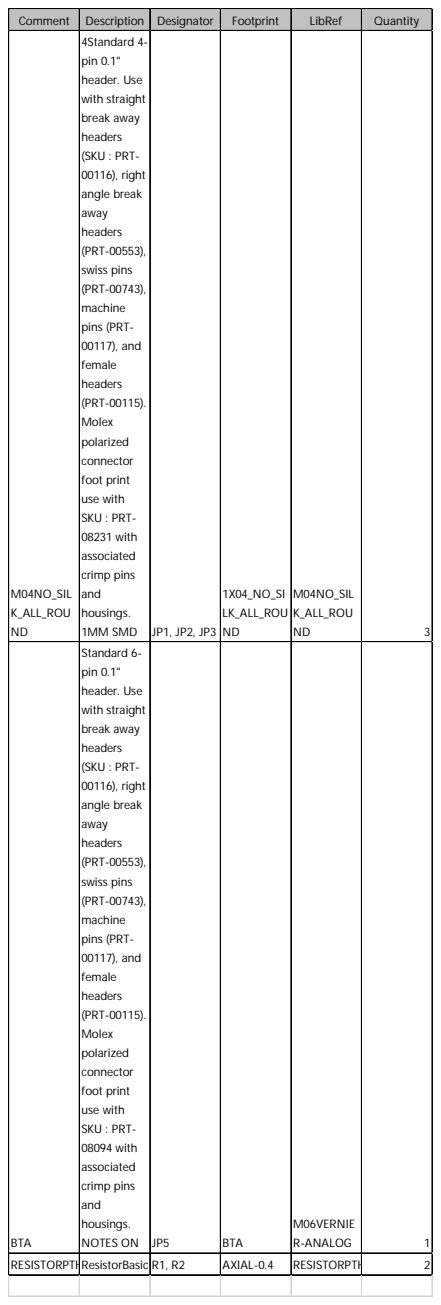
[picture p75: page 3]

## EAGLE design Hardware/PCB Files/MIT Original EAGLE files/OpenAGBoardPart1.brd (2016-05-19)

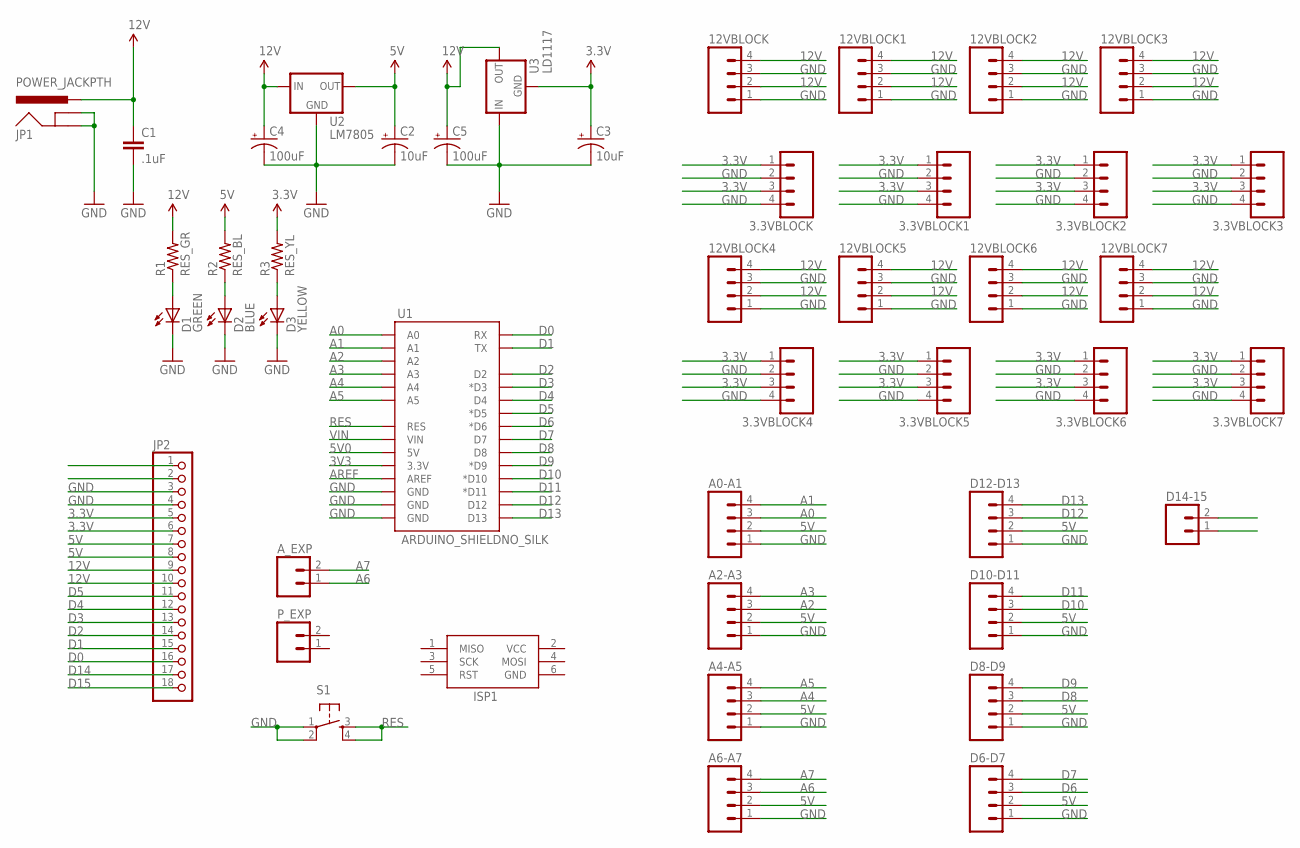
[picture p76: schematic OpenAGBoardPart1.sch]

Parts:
3.3VBLOCK, 3.3VBLOCK1, 3.3VBLOCK2, 3.3VBLOCK3, 3.3VBLOCK4, 3.3VBLOCK5, 3.3VBLOCK6, 3.3VBLOCK7, 12VBLOCK, 12VBLOCK1, 12VBLOCK2, 12VBLOCK3, 12VBLOCK4, 12VBLOCK5, 12VBLOCK6, 12VBLOCK7: M04NO_SILK_ALL_ROUND; 1X04_NO_SILK_ALL_ROUND
A0-A1, A2-A3, A4-A5, A6-A7: M04NO_SILK_ALL_ROUND; 1X04_NO_SILK_ALL_ROUND
A_EXP: M02PTH; 1X02
C1: .1uF; CAP-PTH-SMALL
C2, C3: 10uF; CPOL-RADIAL-10UF-25V
C4, C5: 100uF; CPOL-RADIAL-100UF-25V
D1: GREEN; LED5MM
D2: BLUE; LED5MM
D3: YELLOW; LED5MM
D6-D7, D8-D9, D10-D11, D12-D13: M04NO_SILK_ALL_ROUND; 1X04_NO_SILK_ALL_ROUND
D14-15: M02PTH; 1X02
ISP1: AVRISP-6; AVRISP
JP1: POWER_JACKPTH; POWER_JACK_PTH
JP2: PINHD-1X18-BIG; 1X18-BIG
P_EXP: M02PTH; 1X02
R1: RES_GR; AXIAL-0.4
R2: RES_BL; AXIAL-0.4
R3: RES_YL; AXIAL-0.4
S1: TAC_SWITCHPTH; TACTILE-PTH
U1: ARDUINO_SHIELDNO_SILK; DUEMILANOVE_VIAS
U2: LM7805; TO220-IGO
U3: LD1117; TO220-IGO

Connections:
3.3V: 3.3VBLOCK.1, 3.3VBLOCK.3, 3.3VBLOCK1.1, 3.3VBLOCK1.3, 3.3VBLOCK2.1, 3.3VBLOCK2.3, 3.3VBLOCK3.1, 3.3VBLOCK3.3, 3.3VBLOCK4.1, 3.3VBLOCK4.3, 3.3VBLOCK5.1, 3.3VBLOCK5.3, 3.3VBLOCK6.1, 3.3VBLOCK6.3, 3.3VBLOCK7.1, 3.3VBLOCK7.3, C3.1 (+), JP2.5, JP2.6, R3.P$2 (2), U3.GND
3V3: U1.3.3V
5V: A0-A1.2, A2-A3.2, A4-A5.2, A6-A7.2, C2.1 (+), D6-D7.2, D8-D9.2, D10-D11.2, D12-D13.2, JP2.7, JP2.8, R2.P$2 (2), U2.OUT
5V0: U1.5V
12V: 12VBLOCK.2, 12VBLOCK.4, 12VBLOCK1.2, 12VBLOCK1.4, 12VBLOCK2.2, 12VBLOCK2.4, 12VBLOCK3.2, 12VBLOCK3.4, 12VBLOCK4.2, 12VBLOCK4.4, 12VBLOCK5.2, 12VBLOCK5.4, 12VBLOCK6.2, 12VBLOCK6.4, 12VBLOCK7.2, 12VBLOCK7.4, C1.1, C4.1 (+), C5.1 (+), JP1.PWR, JP2.9, JP2.10, R1.P$2 (2), U2.IN, U3.OUT
A0: A0-A1.3, U1.A0
A1: A0-A1.4, U1.A1
A2: A2-A3.3, U1.A2
A3: A2-A3.4, U1.A3
A4: A4-A5.3, U1.A4
A5: A4-A5.4, U1.A5
A6: A6-A7.3, A_EXP.1
A7: A6-A7.4, A_EXP.2
AREF: U1.AREF
CONTINUITY_STRIP: JP2.1
D0: JP2.16, U1.RX
D1: JP2.15, U1.TX
D2: JP2.14, U1.D2
D3: JP2.13, U1.D3 (*D3)
D4: JP2.12, U1.D4
D5: JP2.11, U1.D5 (*D5)
D6: D6-D7.3, U1.D6 (*D6)
D7: D6-D7.4, U1.D7
D8: D8-D9.3, U1.D8
D9: D8-D9.4, U1.D9 (*D9)
D10: D10-D11.3, U1.D10 (*D10)
D11: D10-D11.4, U1.D11 (*D11)
D12: D12-D13.3, U1.D12
D13: D12-D13.4, U1.D13
D14: D14-15.1, JP2.17
D15: D14-15.2, JP2.18
GND: 3.3VBLOCK.2, 3.3VBLOCK.4, 3.3VBLOCK1.2, 3.3VBLOCK1.4, 3.3VBLOCK2.2, 3.3VBLOCK2.4, 3.3VBLOCK3.2, 3.3VBLOCK3.4, 3.3VBLOCK4.2, 3.3VBLOCK4.4, 3.3VBLOCK5.2, 3.3VBLOCK5.4, 3.3VBLOCK6.2, 3.3VBLOCK6.4, 3.3VBLOCK7.2, 3.3VBLOCK7.4, 12VBLOCK.1, 12VBLOCK.3, 12VBLOCK1.1, 12VBLOCK1.3, 12VBLOCK2.1, 12VBLOCK2.3, 12VBLOCK3.1, 12VBLOCK3.3, 12VBLOCK4.1, 12VBLOCK4.3, 12VBLOCK5.1, 12VBLOCK5.3, 12VBLOCK6.1, 12VBLOCK6.3, 12VBLOCK7.1, 12VBLOCK7.3, A0-A1.1, A2-A3.1, A4-A5.1, A6-A7.1, C1.2, C2.2 (-), C3.2 (-), C4.2 (-), C5.2 (-), D1.K (C), D2.K (C), D3.K (C), D6-D7.1, D8-D9.1, D10-D11.1, D12-D13.1, ISP1.6 (GND), JP1.GND, JP1.GNDBREAK, JP2.3, JP2.4, S1.1, S1.2, U1.GND@0 (GND), U1.GND@1 (GND), U1.GND@2 (GND), U2.GND, U3.IN
unnamed: D1.A, R1.P$1 (1)
unnamed: D2.A, R2.P$1 (1)
unnamed: D3.A, R3.P$1 (1)
RES: S1.3, S1.4, U1.RES
VCC: ISP1.2 (VCC)
VIN: U1.VIN

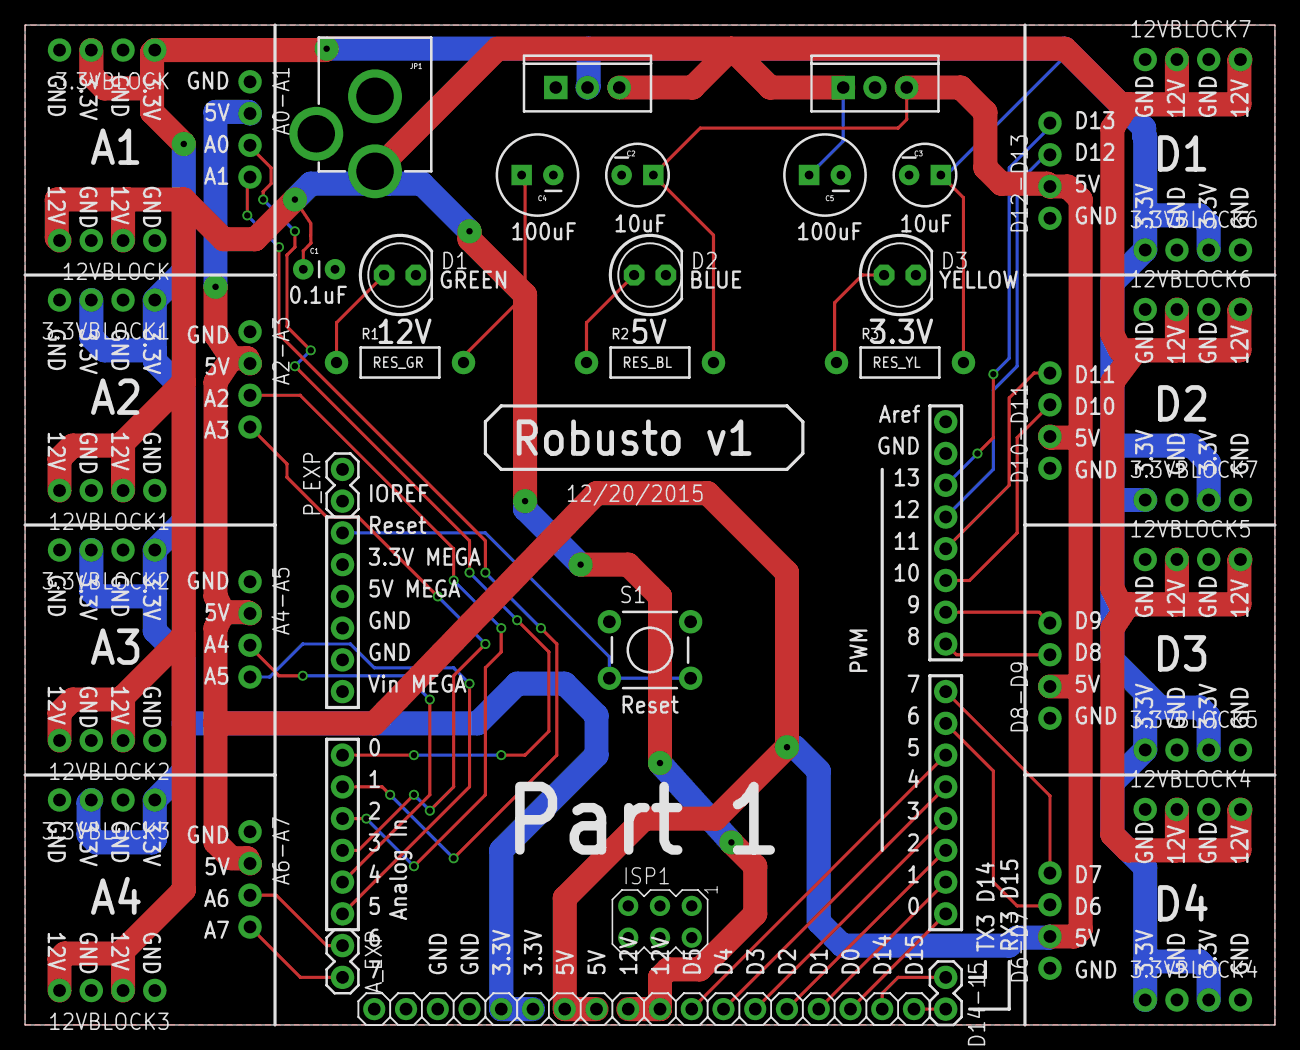
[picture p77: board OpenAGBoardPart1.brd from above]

Board: 2 copper layers, 100.0 x 80.0 mm, 45 parts (0 on the bottom side), 32 nets.

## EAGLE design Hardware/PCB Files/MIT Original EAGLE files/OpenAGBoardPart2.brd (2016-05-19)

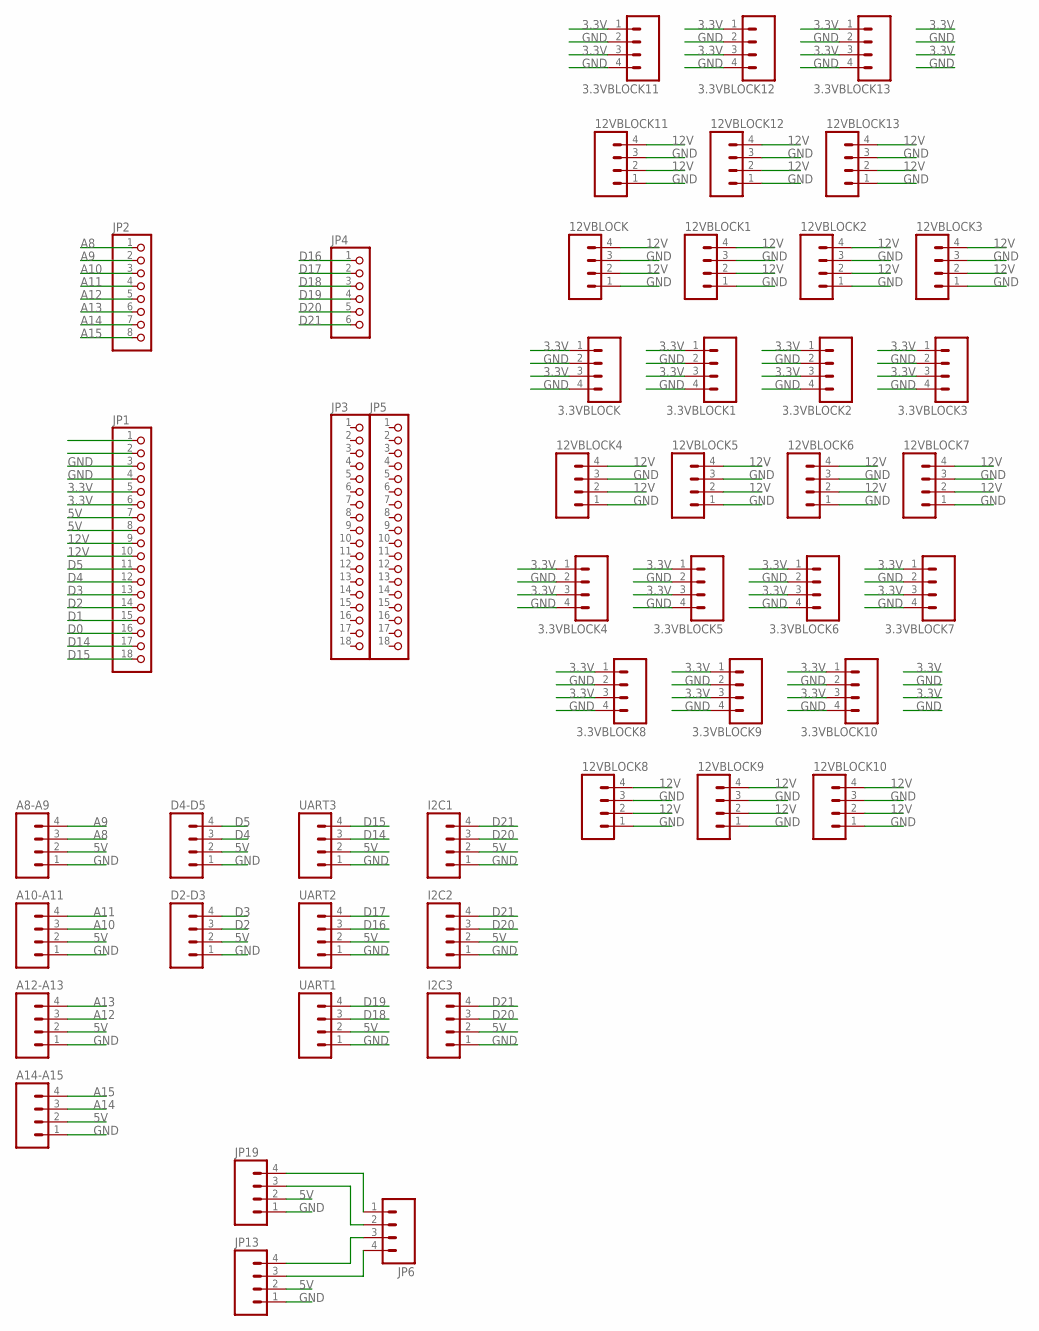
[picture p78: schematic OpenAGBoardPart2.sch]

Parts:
3.3VBLOCK, 3.3VBLOCK1, 3.3VBLOCK2, 3.3VBLOCK3, 3.3VBLOCK4, 3.3VBLOCK5, 3.3VBLOCK6, 3.3VBLOCK7, 3.3VBLOCK8, 3.3VBLOCK9, 3.3VBLOCK10, 3.3VBLOCK11, 3.3VBLOCK12, 3.3VBLOCK13, 12VBLOCK, 12VBLOCK1, 12VBLOCK2, 12VBLOCK3, 12VBLOCK4, 12VBLOCK5, 12VBLOCK6, 12VBLOCK7, 12VBLOCK8, 12VBLOCK9, 12VBLOCK10, 12VBLOCK11, 12VBLOCK12, 12VBLOCK13: M04NO_SILK_ALL_ROUND; 1X04_NO_SILK_ALL_ROUND
A8-A9, A10-A11, A12-A13, A14-A15: M04NO_SILK_ALL_ROUND; 1X04_NO_SILK_ALL_ROUND
D2-D3, D4-D5: M04NO_SILK_ALL_ROUND; 1X04_NO_SILK_ALL_ROUND
I2C1, I2C2, I2C3: M04NO_SILK_ALL_ROUND; 1X04_NO_SILK_ALL_ROUND
JP1, JP3, JP5: PINHD-1X18-BIG; 1X18-BIG
JP2: PINHD-1X8BIG; 1X08-BIG
JP4: PINHD-1X6B; 1X06-BIG
JP6: M04PTH; 1X04
JP13, JP19: M04NO_SILK_ALL_ROUND; 1X04_NO_SILK_ALL_ROUND
UART1, UART2, UART3: M04NO_SILK_ALL_ROUND; 1X04_NO_SILK_ALL_ROUND

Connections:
3.3V: 3.3VBLOCK.1, 3.3VBLOCK.3, 3.3VBLOCK1.1, 3.3VBLOCK1.3, 3.3VBLOCK2.1, 3.3VBLOCK2.3, 3.3VBLOCK3.1, 3.3VBLOCK3.3, 3.3VBLOCK4.1, 3.3VBLOCK4.3, 3.3VBLOCK5.1, 3.3VBLOCK5.3, 3.3VBLOCK6.1, 3.3VBLOCK6.3, 3.3VBLOCK7.1, 3.3VBLOCK7.3, 3.3VBLOCK8.1, 3.3VBLOCK8.3, 3.3VBLOCK9.1, 3.3VBLOCK9.3, 3.3VBLOCK10.1, 3.3VBLOCK10.3, 3.3VBLOCK11.1, 3.3VBLOCK11.3, 3.3VBLOCK12.1, 3.3VBLOCK12.3, 3.3VBLOCK13.1, 3.3VBLOCK13.3, JP1.5, JP1.6
5V: A8-A9.2, A10-A11.2, A12-A13.2, A14-A15.2, D2-D3.2, D4-D5.2, I2C1.2, I2C2.2, I2C3.2, JP1.7, JP1.8, JP13.2, JP19.2, UART1.2, UART2.2, UART3.2
12V: 12VBLOCK.2, 12VBLOCK.4, 12VBLOCK1.2, 12VBLOCK1.4, 12VBLOCK2.2, 12VBLOCK2.4, 12VBLOCK3.2, 12VBLOCK3.4, 12VBLOCK4.2, 12VBLOCK4.4, 12VBLOCK5.2, 12VBLOCK5.4, 12VBLOCK6.2, 12VBLOCK6.4, 12VBLOCK7.2, 12VBLOCK7.4, 12VBLOCK8.2, 12VBLOCK8.4, 12VBLOCK9.2, 12VBLOCK9.4, 12VBLOCK10.2, 12VBLOCK10.4, 12VBLOCK11.2, 12VBLOCK11.4, 12VBLOCK12.2, 12VBLOCK12.4, 12VBLOCK13.2, 12VBLOCK13.4, JP1.9, JP1.10
A8: A8-A9.3, JP2.1
A9: A8-A9.4, JP2.2
A10: A10-A11.3, JP2.3
A11: A10-A11.4, JP2.4
A12: A12-A13.3, JP2.5
A13: A12-A13.4, JP2.6
A14: A14-A15.3, JP2.7
A15: A14-A15.4, JP2.8
D0: JP1.16
D1: JP1.15
D2: D2-D3.3, JP1.14
D3: D2-D3.4, JP1.13
D4: D4-D5.3, JP1.12
D5: D4-D5.4, JP1.11
D14: JP1.17, UART3.3
D15: JP1.18, UART3.4
D16: JP4.1, UART2.3
D17: JP4.2, UART2.4
D18: JP4.3, UART1.3
D19: JP4.4, UART1.4
D20: I2C1.3, I2C2.3, I2C3.3, JP4.5
D21: I2C1.4, I2C2.4, I2C3.4, JP4.6
GND: 3.3VBLOCK.2, 3.3VBLOCK.4, 3.3VBLOCK1.2, 3.3VBLOCK1.4, 3.3VBLOCK2.2, 3.3VBLOCK2.4, 3.3VBLOCK3.2, 3.3VBLOCK3.4, 3.3VBLOCK4.2, 3.3VBLOCK4.4, 3.3VBLOCK5.2, 3.3VBLOCK5.4, 3.3VBLOCK6.2, 3.3VBLOCK6.4, 3.3VBLOCK7.2, 3.3VBLOCK7.4, 3.3VBLOCK8.2, 3.3VBLOCK8.4, 3.3VBLOCK9.2, 3.3VBLOCK9.4, 3.3VBLOCK10.2, 3.3VBLOCK10.4, 3.3VBLOCK11.2, 3.3VBLOCK11.4, 3.3VBLOCK12.2, 3.3VBLOCK12.4, 3.3VBLOCK13.2, 3.3VBLOCK13.4, 12VBLOCK.1, 12VBLOCK.3, 12VBLOCK1.1, 12VBLOCK1.3, 12VBLOCK2.1, 12VBLOCK2.3, 12VBLOCK3.1, 12VBLOCK3.3, 12VBLOCK4.1, 12VBLOCK4.3, 12VBLOCK5.1, 12VBLOCK5.3, 12VBLOCK6.1, 12VBLOCK6.3, 12VBLOCK7.1, 12VBLOCK7.3, 12VBLOCK8.1, 12VBLOCK8.3, 12VBLOCK9.1, 12VBLOCK9.3, 12VBLOCK10.1, 12VBLOCK10.3, 12VBLOCK11.1, 12VBLOCK11.3, 12VBLOCK12.1, 12VBLOCK12.3, 12VBLOCK13.1, 12VBLOCK13.3, A8-A9.1, A10-A11.1, A12-A13.1, A14-A15.1, D2-D3.1, D4-D5.1, I2C1.1, I2C2.1, I2C3.1, JP1.3, JP1.4, JP13.1, JP19.1, UART1.1, UART2.1, UART3.1
unnamed: JP6.1, JP19.4
unnamed: JP6.2, JP19.3
unnamed: JP6.3, JP13.4
unnamed: JP6.4, JP13.3

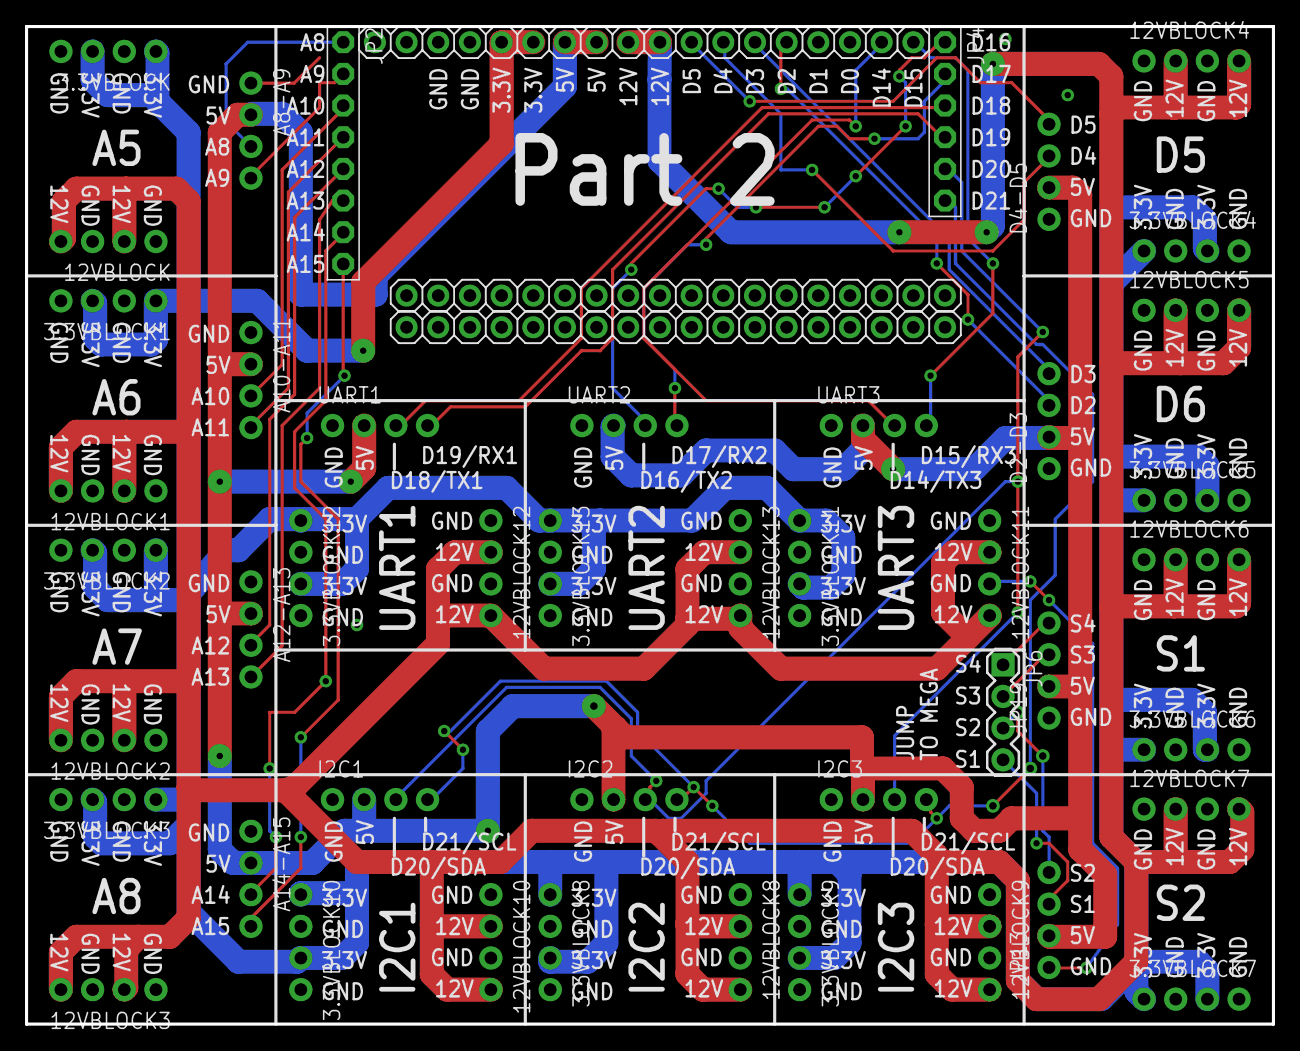
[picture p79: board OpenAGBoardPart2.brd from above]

Board: 2 copper layers, 100.0 x 80.0 mm, 48 parts (0 on the bottom side), 28 nets.

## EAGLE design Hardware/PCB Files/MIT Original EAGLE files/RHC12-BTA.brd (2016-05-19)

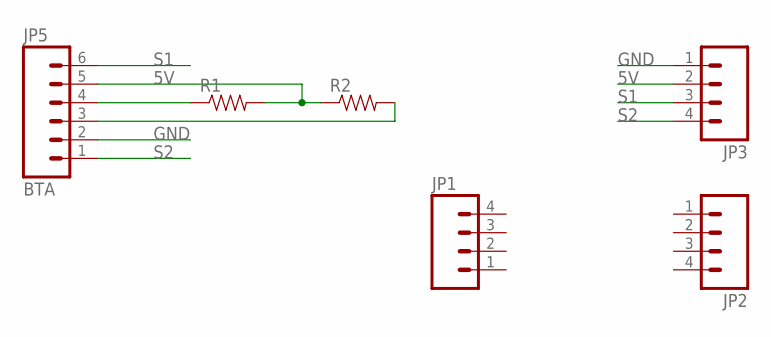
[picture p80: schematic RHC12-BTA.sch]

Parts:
JP1, JP2, JP3: M04NO_SILK_ALL_ROUND; 1X04_NO_SILK_ALL_ROUND
JP5: BTA
R1, R2: RESISTORPTH-1/4W; AXIAL-0.4

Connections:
5V: JP3.2, JP5.5, R1.P$2 (2), R2.P$1 (1)
GND: JP3.1, JP5.2
unnamed: JP5.4, R1.P$1 (1)
unnamed: JP5.3, R2.P$2 (2)
S1: JP3.3, JP5.6
S2: JP3.4, JP5.1

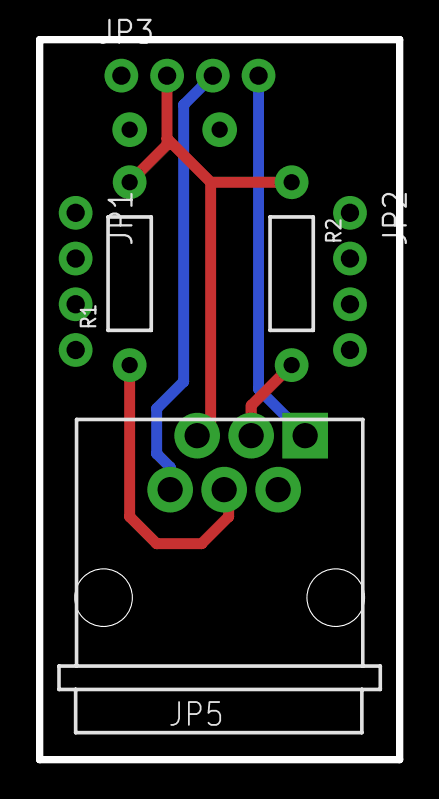
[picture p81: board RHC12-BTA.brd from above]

Board: 2 copper layers, 20.0 x 40.0 mm, 6 parts (0 on the bottom side), 6 nets.

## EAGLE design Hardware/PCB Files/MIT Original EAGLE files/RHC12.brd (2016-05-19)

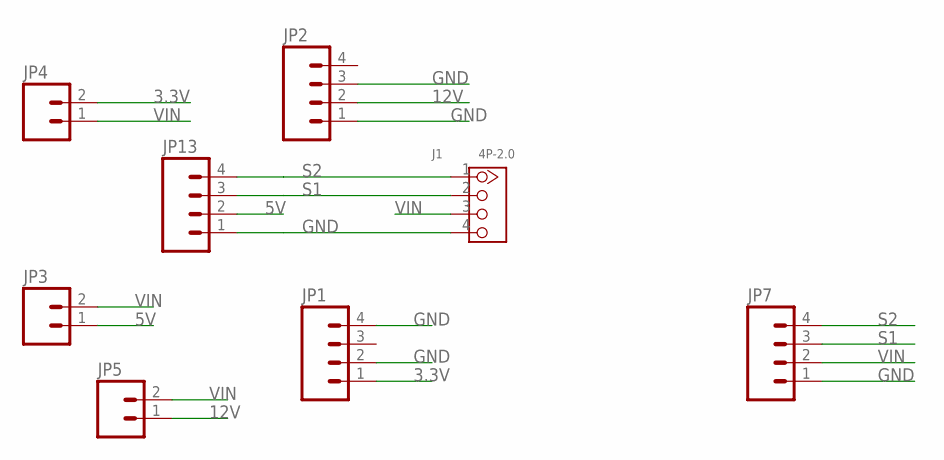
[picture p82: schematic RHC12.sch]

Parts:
J1: 4P-2.0; HW4-2.0
JP1, JP2, JP13: M04NO_SILK_ALL_ROUND; 1X04_NO_SILK_ALL_ROUND
JP3, JP4, JP5: M02PTH; 1X02
JP7: M04PTH; 1X04

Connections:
3.3V: JP1.1, JP4.2
5V: JP3.1, JP13.2
12V: JP2.2, JP5.1
GND: J1.4, JP1.2, JP1.4, JP2.1, JP2.3, JP7.1, JP13.1
S1: J1.2, JP7.3, JP13.3
S2: J1.1, JP7.4, JP13.4
VIN: J1.3, JP3.2, JP4.1, JP5.2, JP7.2

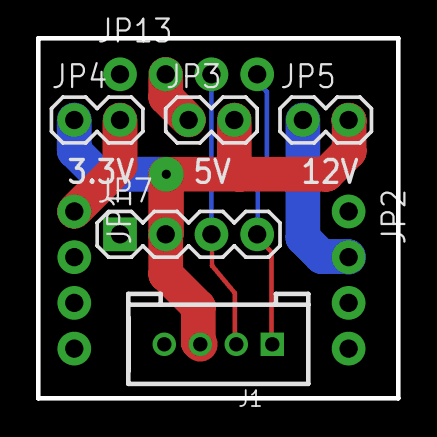
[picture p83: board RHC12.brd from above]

Board: 2 copper layers, 20.0 x 20.0 mm, 8 parts (0 on the bottom side), 7 nets.

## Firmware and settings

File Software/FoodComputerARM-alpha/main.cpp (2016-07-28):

#include "includes.h"

float get_EC(float temperature);
float get_pH();

void update_modbus() //check for request and update relays
{          
        led1 = !led1;  //for debug 
        if (mbs.update(regs, MB_REGS))
        {led3 = !led3;}

        R0 = (regs[MB_9] & (0x0001<<0)); 
        R1 = (regs[MB_9] & (0x0001<<1)); 
        R2 = (regs[MB_9] & (0x0001<<2)); 
        R3 = (regs[MB_9] & (0x0001<<3)); 
        R4 = (regs[MB_9] & (0x0001<<4)); 
        R5 = (regs[MB_9] & (0x0001<<5)); 
        R6 = (regs[MB_9] & (0x0001<<6)); 
        R7 = (regs[MB_9] & (0x0001<<7));
}

int main()
{
    regs[MB_9] = 0xFFFF; //force all relay off       
    
    startMillis(); // milliseconds (arduino like)
    mbs.configure(SLAVE, BAUD, PARITY);
    
    CO2sensor.baud(9600);
    CO2sensor.printf("\nK 2\r\n"); //set the sensor into polling mode
    CO2sensor.scanf(" %[^\n]", &co2string); //dummy - blocking call
            
    lux_sensor.enablePower();
    window_switch.mode(PullUp);
    shell_switch.mode(PullUp);
    water_temp.set_configuration_bits(10); //9bit of resolution so that it is faster
        
    modbus_updater.attach(&update_modbus, 0.1); //visit modbus every 100ms

    while (true) //main thread (updates sensors' status)
    {                                
        led2 = !led2; //for debug        
        
        dht22.readData();
        water_temp.convert_temperature(DS1820::all_devices);         //Start temperature conversion, wait until ready
        water_temperature = water_temp.temperature('c');
        
        CO2sensor.printf("Z\r\n"); //request CO2 reading
        //see: http://stackoverflow.com/questions/16447759/scanf-inside-while-loop-working-only-one-time
        CO2sensor.scanf(" %[^\n]", &co2string); //store it in a buffer (blocking call)                                      
        sscanf(co2string, "%*c %d", &CO2_PPM);   
                        
        regs[MB_0] = CO2_PPM; //air_co2
        regs[MB_1]=  (int)100.0*dht22.ReadHumidity(); //air_humidity
        regs[MB_2]=  (int)100.0*dht22.ReadTemperature(CELCIUS); //air_temp
        regs[MB_3] = (int)100.0*water_temperature;//water_temp in celcius
        regs[MB_4] = (int)100.0*get_EC(water_temperature); //water_ec 
        regs[MB_5] = (int)100.0*get_pH(); //water_ph
        regs[MB_6] = lux_sensor.getLux(); //light_lux
        regs[MB_7]=  window_switch.read(); //window_switch
        regs[MB_8] = shell_switch.read(); //shell_switch                      
    }
}

//For water pH level. Taken from http://www.dfrobot.com/wiki/index.php?title=PH_meter(SKU:_SEN0161)
float get_pH()
{
  float avgValue_;  //Store the average value of the sensor feedback
  float buf_[10],temp_;
  float phValue_;
    
  for(int i=0;i<10;i++)       //Get 10 sample value from the sensor for smooth the value
  { 
    buf_[i]=water_pH.read();
    wait_ms(10);
  }
  for(int i=0;i<9;i++)        //sort the analog from small to large
  {
    for(int j=i+1;j<10;j++)
    {
      if(buf_[i]>buf_[j])
      {
        temp_=buf_[i];
        buf_[i]=buf_[j];
        buf_[j]=temp_;
      }
    }
  }
  avgValue_ = 0.0f;
  for(int i=2;i<8;i++)       //take the average value of 6 center sample
    avgValue_ += buf_[i];
    
  phValue_= avgValue_*5.0f/6.0f; //convert the analog into millivolt
  return 3.5f*phValue_;  
}


//Water Electrical Conductivity Sensor. Taken from http://www.dfrobot.com/wiki/index.php/Analog_EC_Meter_SKU:DFR0300
float get_EC(float temperature)
{  
  float avgValue_;  //Store the average value of the sensor feedback
  float buf_[10], temp_;
  float ECcurrent_; 
    
  for(int i=0;i<10;i++)       //Get 10 sample value from the sensor for smooth the value
  { 
    buf_[i]=water_EC.read();
    wait_ms(10);
  }
  
  for(int i=0;i<9;i++)        //sort the analog from small to large
  {
    for(int j=i+1;j<10;j++)
    {
      if(buf_[i]>buf_[j])
      {
        temp_=buf_[i];
        buf_[i]=buf_[j];
        buf_[j]=temp_;
      }
    }
  }
  
  avgValue_ = 0.0f; for(int i=2;i<8;i++) {avgValue_ += buf_[i];} //take the average value of 6 center sample (don't forget to divide!)
  
  float averageVoltage = avgValue_ * 5000.0f / 6.0f; //divide by 6 because to get average value   
  float TempCoefficient_ = 1.0f + 0.0185f*(temperature - 25.0f);    //temperature compensation formula: fFinalResult(25^C) = fFinalResult(current)/(1.0+0.0185*(fTP-25.0));
  float CoefficientVoltage_ = averageVoltage / TempCoefficient_;

  if      (CoefficientVoltage_ <= 448.0f)   {ECcurrent_ = 6.84f*CoefficientVoltage_ - 64.320f;}    //1ms/cm<EC<=3ms/cm
  else if (CoefficientVoltage_ <= 1457.0f)  {ECcurrent_ = 6.98f*CoefficientVoltage_ - 127.00f;}    //3ms/cm<EC<=10ms/cm
  else                                     {ECcurrent_ = 5.30f*CoefficientVoltage_ + 2278.0f;}    //10ms/cm<EC<20ms/cm
            
  return ECcurrent_/=1000.0f;    //convert us/cm to ms/cm
}

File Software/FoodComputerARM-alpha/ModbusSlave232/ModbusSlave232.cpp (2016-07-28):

/* 		
 Modified by Afdhal: arduino library so that it can be used on mbed.
 
 Original message:
 Modbus over serial line - RTU Slave Arduino Sketch 
 
 By Juan Pablo Zometa : jpmzometa@gmail.com
 http://sites.google.com/site/jpmzometa/
 Samuel Marco: sammarcoarmengol@gmail.com
 and Andras Tucsni.
 
 These functions implement functions 3, 6, and 16 (read holding registers,
 preset single register and preset multiple registers) of the 
 Modbus RTU Protocol, to be used over the Arduino serial connection.
 
 This implementation DOES NOT fully comply with the Modbus specifications.
 
 This Arduino adaptation is derived from the work
 By P.Costigan email: phil@pcscada.com.au http://pcscada.com.au
 
 These library of functions are designed to enable a program send and
 receive data from a device that communicates using the Modbus protocol.
 
 Copyright (C) 2000 Philip Costigan  P.C. SCADA LINK PTY. LTD.
 
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
 The functions included here have been derived from the 
 Modicon Modbus Protocol Reference Guide
 which can be obtained from Schneider at www.schneiderautomation.com.
 
 This code has its origins with 
 paul@pmcrae.freeserve.co.uk (http://www.pmcrae.freeserve.co.uk)
 who wrote a small program to read 100 registers from a modbus slave.
 
 I have used his code as a catalist to produce this more functional set
 of functions. Thanks paul.
 */


//#include "Arduino.h" //afdhal


#include "millis.h"
#include "MODSERIAL.h" //afdhal
MODSERIAL pc(USBTX, USBRX); // tx, rx //afdhal

#ifndef ModbusSlave232_h
	#include "ModbusSlave232.h"
#endif


/****************************************************************************
 * BEGIN MODBUS RTU SLAVE FUNCTIONS
 ****************************************************************************/

/* constants */
enum { 
        MAX_READ_REGS = 0x7D, 
        MAX_WRITE_REGS = 0x7B, 
        MAX_MESSAGE_LENGTH = 256 
};


enum { 
        RESPONSE_SIZE = 6, 
        EXCEPTION_SIZE = 3, 
        CHECKSUM_SIZE = 2 
};

/* exceptions code */
enum { 
        NO_REPLY = -1, 
        EXC_FUNC_CODE = 1, 
        EXC_ADDR_RANGE = 2, 
        EXC_REGS_QUANT = 3, 
        EXC_EXECUTE = 4 
};

/* positions inside the query/response array */
enum { 
        SLAVE = 0, 
        FUNC, 
        START_H, 
        START_L, 
        REGS_H, 
        REGS_L, 
        BYTE_CNT 
};


/* enum of supported modbus function codes. If you implement a new one, put its function code here ! */
enum { 
        FC_READ_REGS  = 0x03,   //Read contiguous block of holding register
        FC_WRITE_REG  = 0x06,   //Write single holding register
        FC_WRITE_REGS = 0x10    //Write block of contiguous registers
};

/* supported functions. If you implement a new one, put its function code into this array! */
const unsigned char fsupported[] = { FC_READ_REGS, FC_WRITE_REG, FC_WRITE_REGS };


/*
CRC
 
 INPUTS:
 	buf   ->  Array containing message to be sent to controller.            
 	start ->  Start of loop in crc counter, usually 0.
 	cnt   ->  Amount of bytes in message being sent to controller/
 OUTPUTS:
 	temp  ->  Returns crc byte for message.
 COMMENTS:
 	This routine calculates the crc high and low byte of a message.
 	Note that this crc is only used for Modbus, not Modbus+ etc. 
 ****************************************************************************/

unsigned int ModbusSlave232::crc(unsigned char *buf, unsigned char start,
unsigned char cnt) 
{
        unsigned char i, j;
        unsigned temp, temp2, flag;

        temp = 0xFFFF;

        for (i = start; i < cnt; i++) {
                temp = temp ^ buf[i];

                for (j = 1; j <= 8; j++) {
                        flag = temp & 0x0001;
                        temp = temp >> 1;
                        if (flag)
                                temp = temp ^ 0xA001;
                }
        }

        /* Reverse byte order. */
        temp2 = temp >> 8;
        temp = (temp << 8) | temp2;
        temp &= 0xFFFF;

        return (temp);
}




/***********************************************************************
 * 
 * 	The following functions construct the required query into
 * 	a modbus query packet.
 * 
 ***********************************************************************/

/* 
 * Start of the packet of a read_holding_register response 
 */
void ModbusSlave232::build_read_packet(unsigned char function,
unsigned char count, unsigned char *packet) 
{
        packet[SLAVE] = slave;
        packet[FUNC] = function;
        packet[2] = count * 2;
} 

/* 
 * Start of the packet of a preset_multiple_register response 
 */
void ModbusSlave232::build_write_packet(unsigned char function,
unsigned int start_addr, 
unsigned char count,
unsigned char *packet) 
{
        packet[SLAVE] = slave;
        packet[FUNC] = function;
        packet[START_H] = start_addr >> 8;
        packet[START_L] = start_addr & 0x00ff;
        packet[REGS_H] = 0x00;
        packet[REGS_L] = count;
} 

/* 
 * Start of the packet of a write_single_register response 
 */
void ModbusSlave232::build_write_single_packet(unsigned char function,
        unsigned int write_addr, unsigned int reg_val, unsigned char* packet) 
{
        packet[SLAVE] = slave;
        packet[FUNC] = function;
        packet[START_H] = write_addr >> 8;
        packet[START_L] = write_addr & 0x00ff;
        packet[REGS_H] = reg_val >> 8;
        packet[REGS_L] = reg_val & 0x00ff;
} 


/* 
 * Start of the packet of an exception response 
 */
void ModbusSlave232::build_error_packet( unsigned char function,
unsigned char exception, unsigned char *packet) 
{
        packet[SLAVE] = slave;
        packet[FUNC] = function + 0x80;
        packet[2] = exception;
} 


/*************************************************************************
 * 
 * modbus_query( packet, length)
 * 
 * Function to add a checksum to the end of a packet.
 * Please note that the packet array must be at least 2 fields longer than
 * string_length.
 **************************************************************************/

void ModbusSlave232::modbus_reply(unsigned char *packet, unsigned char string_length) 
{
        int temp_crc;

        temp_crc = crc(packet, 0, string_length);
        packet[string_length] = temp_crc >> 8;
        string_length++;
        packet[string_length] = temp_crc & 0x00FF;
} 



/***********************************************************************
 * 
 * send_reply( query_string, query_length )
 * 
 * Function to send a reply to a modbus master.
 * Returns: total number of characters sent
 ************************************************************************/
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

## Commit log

2016-05-19 Added hardware and UK suppliers
    [BOM food computer UK Suppliers.xlsx, Base SubAssem.SLDASM, Double magnet SubAssem.SLDASM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]
2016-05-19 added PCB and microcontroller software
    this needs going through to make sure it is up to date
    [OpenAGBoardPart1.brd, OpenAGBoardPart1.sch, OpenAGBoardPart2.brd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]
2016-05-19 Converted PCB files to Altium
    [OpenAGBoardPart1.PcbDoc, OpenAGBoardPart1.PrjPcb, OpenAGBoardPart1.SchDoc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]
2016-05-19 added photos of PCBs and converted to Altium Smart PDF
2016-06-16 added schematic for protoshield from http://adrianllu.com/category/food-computer/
2016-06-16 (updated to hi-res) added schematic for protoshield from http://adrianllu.com/category/food-computer/
2016-07-04 Library issue fixed (Wire.h).
2016-07-28 Added ARM with MODBUS (mbed).
2016-08-08 added node-red flow V1

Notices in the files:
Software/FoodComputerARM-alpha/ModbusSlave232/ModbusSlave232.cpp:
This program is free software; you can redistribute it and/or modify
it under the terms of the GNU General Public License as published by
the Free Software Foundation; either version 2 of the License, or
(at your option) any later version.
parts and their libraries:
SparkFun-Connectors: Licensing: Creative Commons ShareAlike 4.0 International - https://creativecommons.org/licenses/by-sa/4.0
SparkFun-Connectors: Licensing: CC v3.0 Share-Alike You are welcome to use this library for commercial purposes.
